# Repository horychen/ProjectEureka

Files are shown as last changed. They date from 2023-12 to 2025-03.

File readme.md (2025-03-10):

# ProjectEureka!--A Multi-phase Motor Drive Design for Robot or Maglev systems

ProjectEureka seeks to streamline the intricate design of robot systems, including communication, cable arrangements, and synchronization, by integrating several motor drivers (up to four) with a single microcontroller (DSP2837xD). This can also be utilized as a testing platform for bearingless motor or any other kind of AC motors. For access to example codes, please visit the following link: [here](https://github.com/horychen/ProjectPanGu-C) for cpu01 code, and [here](https://github.com/horychen/ProjectPanGuCpu2) for cpu02 code. Displayed below is an image representing the previous version.

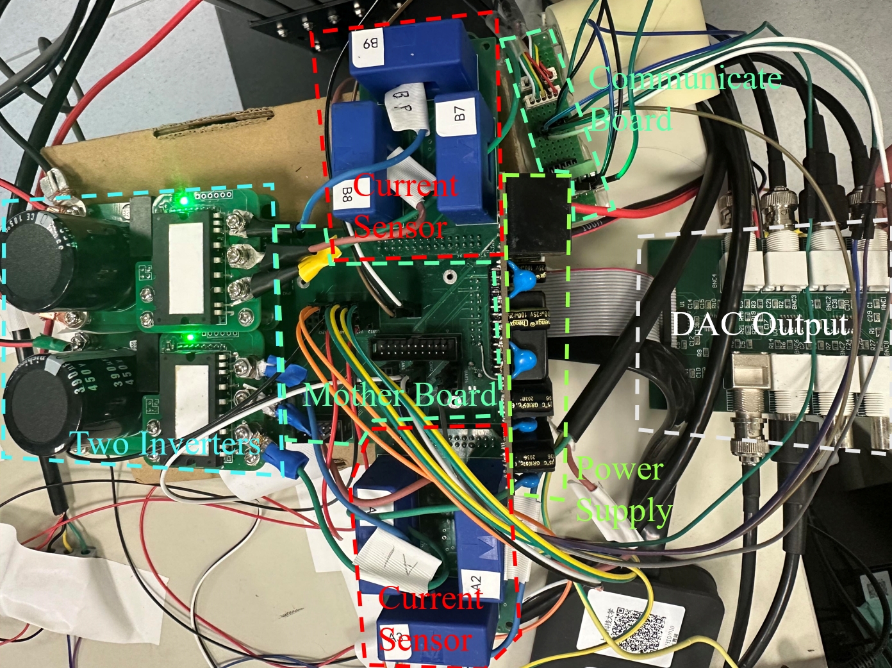
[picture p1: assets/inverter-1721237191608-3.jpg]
inverter-3d-view


## Software

We have been shifting from Altium Designer to KiCAD.

## Characteristics

**Multi-board modulized design is adopted in Project Eureka!.** Project Eureka! includes:

1. Current sensor(LA55-P) [📂 PCBProject_SensorLEM](PCBProject_SensorLEM)
2. DAC data collect board(MAX5725)[📂PCBProject_SPI_MAX5307_DAC](PCBProject_SPI_MAX5307_DAC)
3. RS422/RS423 communication board [📂PCBProject_Encoder](PCBProject_Encoder)
4. Inverters (FNC42060F) [📂PCBProject_InverterFNC42060F](PCBProject_InverterFNC42060F)
5. Auxiliary power supply [📂PCBProject_Power](PCBProject_Power)
6. Mother board that connected all the boards above [📂PCBProject_Extension28377dBGA](PCBProject_Extension28377dBGA)
7. CAN/SCI/USB communication board[📂PCBProject_Can_SCI_USB](PCBProject_Can_SCI_USB)
8. RS485 communication board [📂PCBProject_Happy485](PCBProject_Happy485)

This means:

1. Convenient alternative for replacing one's own projects or addressing shortages of components.
2. Utilize a single board design in their own design.
3. Quick update and easy for collaboration (KiCAD 8 supports git now).

**ProjectEureka can drive at most four AC motors.** Thanks to the TMS320F28377D from TI, ProjectEureka can drive at most four AC motors by adding necessary inverter blocks and corresponding current sensors, which means:

1. Facilitates communication and synchronization among motors.
2. Suitable for organizing cables in a user-friendly manner.

## Liscence
GPLv3

## Other Similar Projects

Odrive and VESC are two famous projects that support the control of a three-phase motor.
There are inverter designs that are compatible with them, see e.g., [Axiom](https://hackaday.io/project/164932-axiom-100kw-motor-controller). Other similar but less known hardwares can also be found, see e.g., [moteus-c1](https://jpieper.com/2024/04/30/moteus-c1/). Yet another project I recently found is [STMBL](https://github.com/rene-dev/stmbl?tab=readme-ov-file) for STM32 microprocessor.

ProjectEureka! is, however, focusing on the more advanced topic of a complicated system that requires extendable hardwares.
In this sense, there is indeed one similar purpose project that is based on Xilinx, i.e., [the AMDC platform from the group of Prof. Eric L. Severson](https://amdc.dev/). See also [its doc](https://docs.amdc.dev/getting-started/user-guide/host-interface/index.html) and [its blog post](https://severson.wempec.wisc.edu/2022/02/11/introducing-the-advanced-motor-drive-controller/).

As a comparison, ProjectEureka! currently only supports 28379D that has one CLB module of a very limited FPGA capability.

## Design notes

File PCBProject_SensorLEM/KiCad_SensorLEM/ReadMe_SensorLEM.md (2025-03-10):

# ReadMe_SensorLEM

下面这个是完整的驱动板，其中两条蓝色的器件是电流传感器，**<font color=red>左边</font>**的名称为对应到ProjectEureka\PCBProject_SensorLEM\KiCad_SensorLEM文件下的**<font color=red>SensorLEM1</font>**，然后**<font color=gree>右边</font>**的电流传感器对应到ProjectEureka\PCBProject_SensorLEM\KiCad_SensorLEM文件下的**<font color=gree>SensorLEM2</font>**。

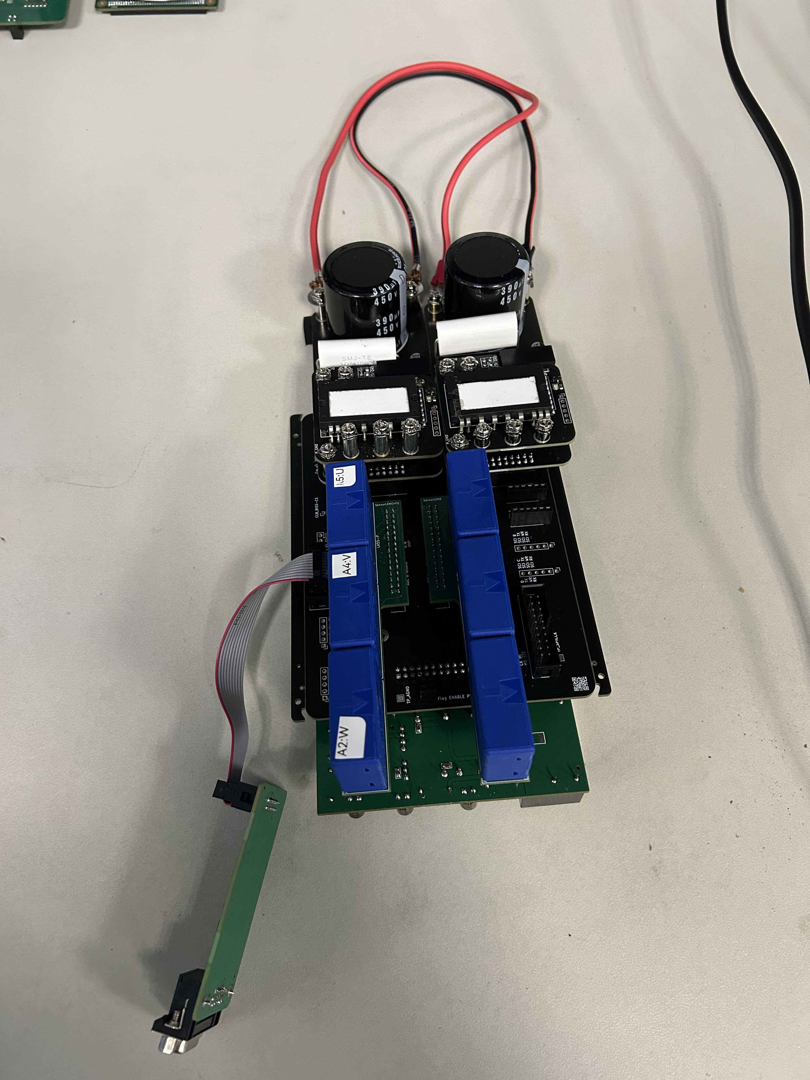
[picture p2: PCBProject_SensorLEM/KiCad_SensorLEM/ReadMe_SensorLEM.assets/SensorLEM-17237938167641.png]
SensorLEM


具体电路图就请看ProjectEureka\PCBProject_SensorLEM\KiCad_SensorLEM文件下的kicad文件。

****

<font color=red>我是红色</font>

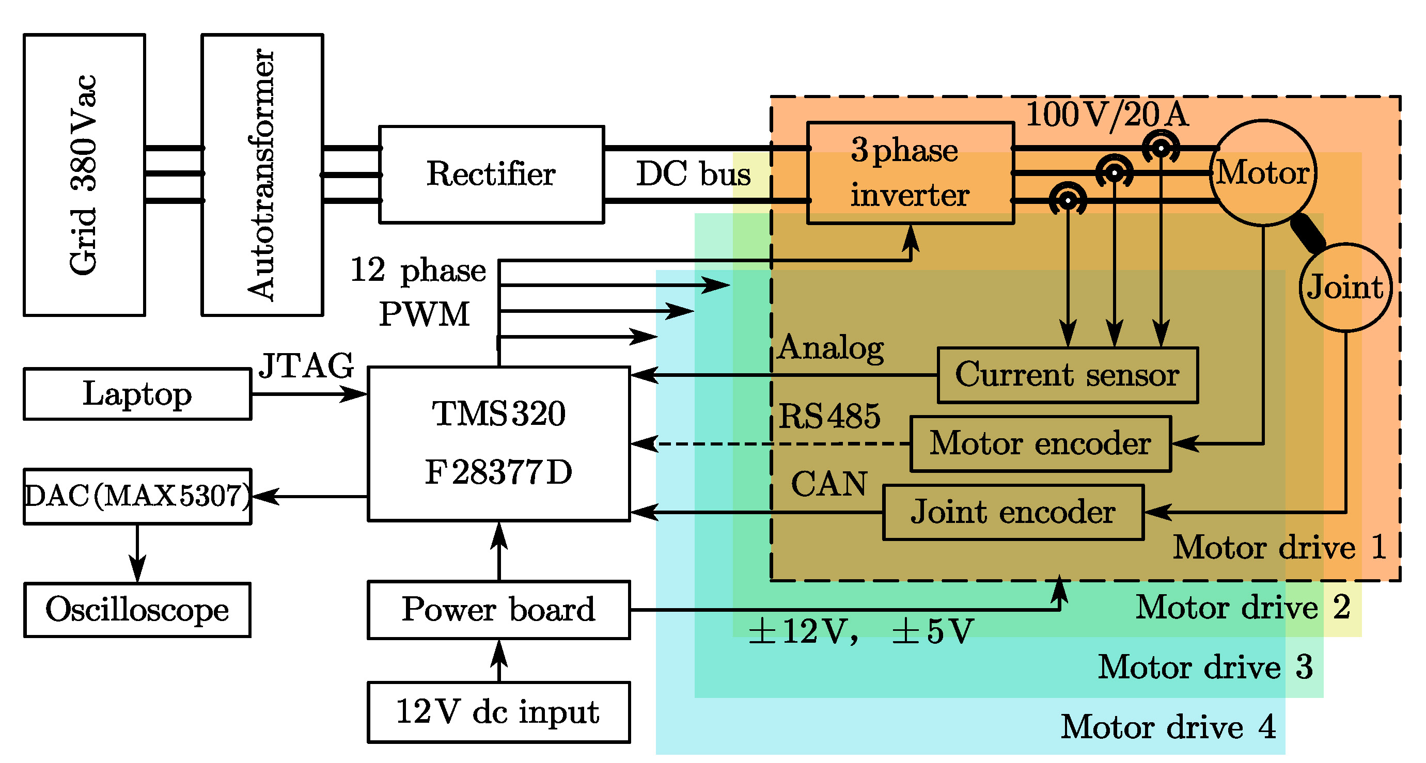
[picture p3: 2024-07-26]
assets/Block_Diagram.jpg

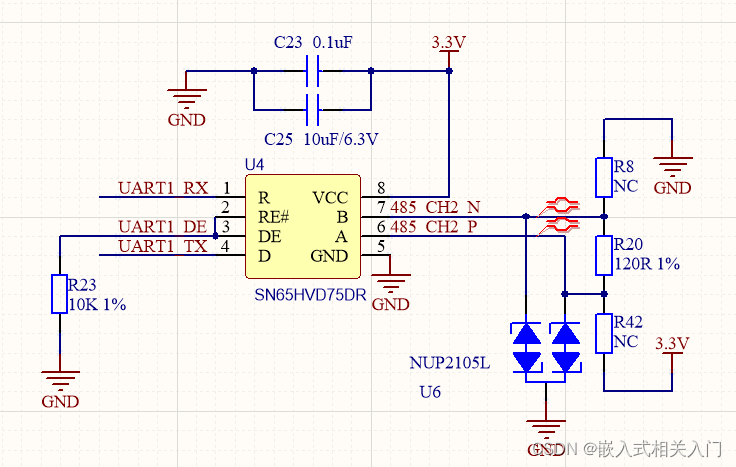
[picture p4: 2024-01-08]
PCBProject_Happy485/datasheet/野生原理图1.png

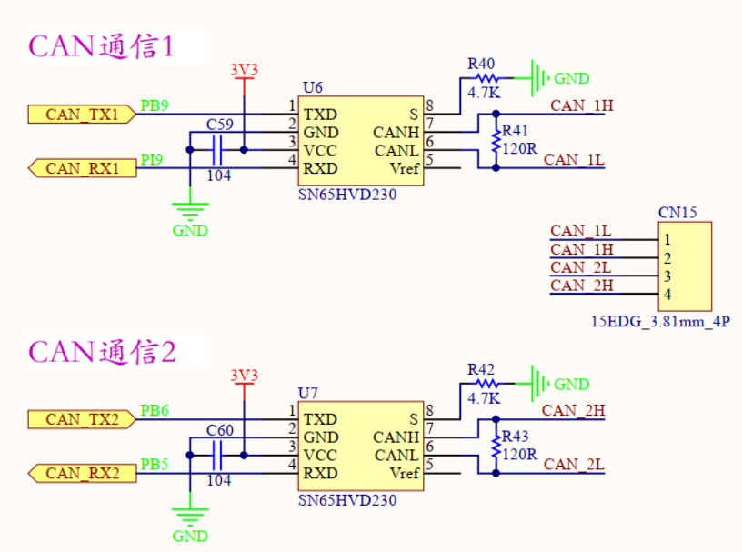
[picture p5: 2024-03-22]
PCBProject_Extension28377dBGA/ExtensionSimple2/Refs/CAN收发器SN65HVD230,实际应用案例分析.png

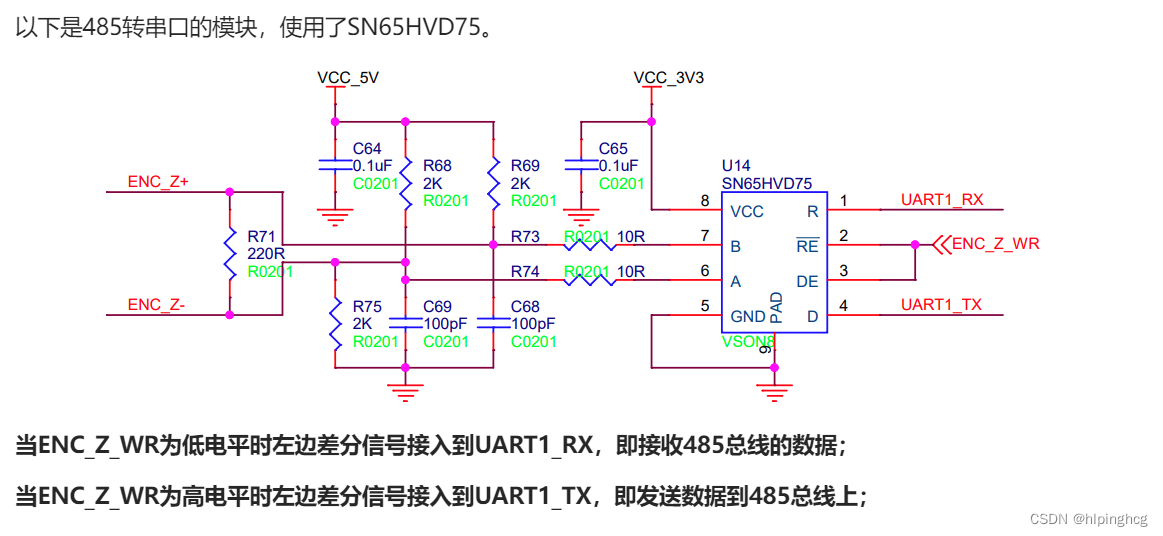
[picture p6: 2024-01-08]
PCBProject_Happy485/datasheet/野生原理图2.png

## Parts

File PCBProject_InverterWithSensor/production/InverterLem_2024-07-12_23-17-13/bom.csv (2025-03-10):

Designator | Footprint | Quantity | Value | LCSC Part #
+12 | TestPoint_Pad_D1.0mm | 1 | +12
+5v | TestPoint_Pad_D1.0mm | 1 | Test5V
-12 | TestPoint_Pad_D1.0mm | 1 | -12
15V | TestPoint_Pad_D1.0mm | 1 | Test15V
1A | TestPoint_Pad_D1.0mm | 1 | OPWM1A
1B | TestPoint_Pad_D1.0mm | 1 | OPWM1B
2A | TestPoint_Pad_D1.0mm | 1 | OPWM2A
2B | TestPoint_Pad_D1.0mm | 1 | OPWM2B
3A | TestPoint_Pad_D1.0mm | 1 | OPWM3A
3B | TestPoint_Pad_D1.0mm | 1 | OPWM3B
A1, A2, A3 | XDCR_LA55-P | 3 | LA55-P
A6 | VRB_S-6WR3 | 1 | VRB1215S-6WR3
AGND | TestPoint_Pad_D1.0mm | 1 | AGND
C1, C2, C3, C7, C8, C9 | 0603 | 6 | 47nf
C19, C59, C60, C61, C62 | CP_Radial_D16.0mm_P7.50mm | 5 | 47uF/450V
C20 | CP_EIA-3528-21_Kemet-B_Pad1.50x2.35mm_HandSolder | 1 | 15uF 50V Tantalum
C23 | 0603 | 1 | 10nF
C24 | 0603 | 1 | 1nf
C25 | CP_EIA-6032-28_Kemet-C_Pad2.25x2.35mm_HandSolder | 1 | 68uF 16V Tantalum
C27, C38, C39 | 0603 | 3 | 100nf
C4, C5, C6 | 0603 | 3 | 4.7uF
C40, C41, C42, C45, C46, C47 | 0603 | 6 | 2.2uf
C43, C44, C49, C54, C55, C57 | 0603 | 6 | 100pf
C48, C50, C51, C52, C56 | 0805 | 5 | 100nF
C53 | CP_Elec_6.3x7.7 | 1 | 100uf 50V
C58 | CP_Elec_5x5.4 | 1 | 22uf 25V
D1, D2 | D_SMA | 2 | 1N5819
D3 | 0805 | 1 | LEDRED
IC1, IC2, IC3 | SOIC-8_7.5x5.85mm_P1.27mm | 3 | TLP2270_D4-LF4,E
J1 | M3_smt | 1 | Phase 1
J2 | IDC-Header_2x10_P2.54mm_Vertical_SMD | 1 | DSP
J3 | M3_smt | 1 | Phase 2
J4 | M3_smt | 1 | Phase 3
J5 | PinSocket_1x02_P2.54mm_Vertical | 1 | Fan
J6 | M3_smt | 1 | DC_BUS
J7 | M3_smt | 1 | GND
J9 | PinSocket_1x02_P2.54mm_Vertical | 1 | Conn_01x02_Pin
L1 | L_6.3x6.3_H3 | 1 | 47uH
Q1 | FNC42060F | 1 | FNC42060F
Q2 | SOT-23-3 | 1 | FMMT618TA
R11, R12 | 0805 | 2 | 2M
R13, R14, R16, R21, R22, R23 | 0603 | 6 | 750R
R24, R25 | 2512 | 2 | 8mR
R26 | 1206 | 1 | 2k
R27, R28, R29, R30, R31, R32 | 0603 | 6 | 100R
R33, R34 | 0603 | 2 | 10K
R35 | 0603 | 1 | 2K
R36 | 0603 | 1 | 301R
RB1, RB2, RB3, RB4, RB5, RB6 | 0805 | 6 | 0R
U2 | SOIC-8_3.9x4.9mm_P1.27mm | 1 | LM2675M-5.0
Z1, Z2, Z3 | MELF_DO-213AB | 3 | ZM4746A-GS08

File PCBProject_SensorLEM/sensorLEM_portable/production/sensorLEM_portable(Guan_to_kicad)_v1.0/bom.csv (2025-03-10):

Designator | Footprint | Quantity | Value | LCSC Part #
A1, A4, A6 | SOT95P280X100-5N | 3 | LTC6240HV
A2, A3, A5 | XDCR_LA55-P | 3 | LA55-P
A7, A8 | VRB_S-6WR3 | 2 | VRB1215S-6WR3
BNC1, BNC2, BNC3 | BNC | 3 | BNC
C1, C15, C20, C3, C32, C34, C45 | 0805 | 7 | 105
C10, C12, C18, C24, C37, C38, C42, C48, C49, C54 | 0805 | 10 | 104
C11, C19, C23, C33, C41, C6 | 0805 | 6 | 47nf
C13, C14, C21, C26, C31, C39, C43, C44, C7 | 0805 | 9 | 103
C16, C2, C46, C5, C60 | CAP/6.4mm - | 5 | 100uf 25V 贴片铝电解
C17, C4, C47, C51, C8 | 1206 (钽电容) | 5 | 22uf 16V
C22, C40, C9 | 0805 | 3 | 101
C35, C36 | 1206 (钽电容) | 2 | 106 25V
C52, C55, C56 | 0805 | 3 | 102
D4 | l0805 | 1 | LED0
J1 | SHDR10W50P254_2X5_2020X850X920P | 1 | HIF3FC-10PA-2.54DSA_71_
J2, J3 | 接地柱M3 | 2 | Header 2
R1, R11, R13, R16, R6, R8 | 0805 | 6 | 20k
R10, R15, R4 | 0805 | 3 | 470R
R12, R14, R17, R3, R7, R9 | 0805 | 6 | 10k
R18 | 0805 | 1 | 1k
R19, R20, R21, RB1, RB2, RB3 | 0805 | 6 | 0R
RM1, RM2, RM3 | 2512 | 3 | 24R 1%精度
U1 | URB-YMD-15WR3 | 1 | URB2405YMD-15W
U2 | VRB_S-6WR3 | 1 | VRB1205S-6WR3
U4 | SOIC-8 | 1 | ADR423ARZ

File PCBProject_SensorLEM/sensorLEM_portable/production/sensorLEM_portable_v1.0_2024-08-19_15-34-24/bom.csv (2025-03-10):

Designator | Footprint | Quantity | Value | LCSC Part #
A1, A2, A3, A4, A5, A6 | LEM_LA 55-P | 6 | LA55-P
BNC1, BNC2, BNC3, BNC4, BNC5, BNC6 | CPBNCPC010 | 6 | BNC
C1, C15, C7, C8 | CAP-TH_L7.5-W4.5-P10.00-D0.6 | 4 | 1nF
C10, C14, C3, C5 | 0805 | 4 | 105
C11, C12, C16, C17, C18, C25, C26, C27, C31, C32, C33, C6 | 0805 | 12 | 47nf
C13, C2, C34, C4, C9 | CAP_6.4mm | 5 | 100uf 25V 贴片铝电解
C19, C20, C21, C22, C23, C24 | 0805 | 6 | 4.7uF
CN1 | CONN-TH_4P-P3.81_DB2EVC-3.81-4P | 1 | DB2EVC-3.81-4P-GN
D1 | LED0805 | 1 | LED0
R1, R19, R2, R20, R21, R3, RB1, RB10, RB11, RB12, RB2, RB3, RB4, RB5, RB6, RB7, RB8, RB9 | 0805 | 18 | 0R
R6 | 0805 | 1 | 4.7k
RM1, RM2, RM3, RM4, RM5, RM6 | 2512 | 6 | 24R 1%精度
U1, U2 | SIP,22x9.5mm | 2 | VRB1212S-6WR3
U3 | PWRM-TH_MORNSUN_FT-AX1D | 1 | FT-AX1D

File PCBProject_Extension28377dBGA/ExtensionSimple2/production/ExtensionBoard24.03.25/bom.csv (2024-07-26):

Designator | Footprint | Quantity | Value | LCSC Part #
C1, C15, C16, C2, C3, C4, C9 | 0805 | 7 | 104
C10, C11, C12 | 0805 | 3 | 103
C13, C14 | 0603 | 2 | 0.1uF
C5, C6, C7, C8 | 0805 | 4 | 102
CAN1, CAN2, SPI2, UART3, UART4 | PinSocket_2x04_P2.54mm_Vertical | 5 | Conn_02x04_Counter_Clockwise
D1, D2 | SOT-23 | 2 | BAR43S
D3 | 0805 | 1 | LEDRED
DI1 | PinSocket_2x02_P2.54mm_Vertical | 1 | Conn_02x02_Counter_Clockwise
DSP1 | DSP_240_SMD | 1 | ~
INC1, SPI1 | IDC-Header_2x10_P2.54mm_Vertical | 2 | HIF3FC-20PA-2.54DSA
IPM1, IPM2 | PinSocket_2x08_P2.54mm_Vertical | 2 | Conn_02x08_Top_Bottom
J1 | IDC-Header_2x05_P2.54mm_Vertical | 1 | Conn_02x05_Odd_Even
J2, J3 | PinSocket_2x02_P2.54mm_Vertical | 2 | Conn_01x02_Pin
J4 | PinSocket_1x05_P2.54mm_Vertical | 1 | CAN_1_CONNECT
J5 | PinSocket_1x04_P2.54mm_Vertical | 1 | RS485_1_CONNECT
J6 | PinSocket_1x05_P2.54mm_Vertical | 1 | CAN_2_CONNECT
J7 | PinSocket_1x04_P2.54mm_Vertical | 1 | RS485_2_CONNECT
LEM1, LEM2, POWER1 | PinSocket_2x15_P2.54mm_Vertical | 3 | HIF3FC-30PA-2.54DSA
N1 | SOIC14_M | 1 | MCP6024
Q1 | SOT-23 | 1 | FMMT618TA
R1, R10, R11, R12, R2, R3, R4, R48, R49, R5, R6, R7, R8, R9 | 0805 | 14 | 4.7k
R13, R14, R15, R16, RU3 | 0805 | 5 | 0R
R17, R18, R19, R20, R27, R28, R29, R32, R33 | 0805 | 9 | 10K
R21, R22, R24, R31 | 0805 | 4 | 1K
R23 | 0805 | 1 | 100R
R25 | 0805 | 1 | 1.69K/1%
R26 | 0805 | 1 | 3.3K/1%
R30 | 0805 | 1 | 2K
R34, R35, R39, R40, R41, R42, R46, R47 | 0603 | 8 | 10K
R36, R43 | 0603 | 2 | 120R
R37, R38, R44, R45 | 0402 | 4 | 10R
SCI_RS485_1, SCI_RS485_2 | SOIC127P600X175-8N | 2 | SN65HVD75D
TP1, TP10, TP11, TP12, TP2, TP3, TP4, TP5, TP6, TP7, TP8, TP9, VDC_BUS1, VDC_BUS2 | TestPoint_Pad_2.0x2.0mm | 14 | TP-黄色测试点
U1, U2 | TSSOP-20 | 2 | SN74ABT541
U4, U5 | SOIC-8_3.9x4.9mm_P1.27mm | 2 | SN65HVD230

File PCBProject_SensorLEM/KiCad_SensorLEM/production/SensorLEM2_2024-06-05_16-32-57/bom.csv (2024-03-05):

Designator | Footprint | Quantity | Value | LCSC Part #
A1, A3, A6 | SOT95P280X100-5N | 3 | LTC6240HV
A2, A4, A5 | XDCR_LA55-P | 3 | LA55-P
C1, C10, C18, C20, C27, C9 | 0805 | 6 | 105
C11, C13, C16, C2, C21, C25, C26, C4, C6 | 0805 | 9 | 103
C12, C23, C3 | 0805 | 3 | 101
C14, C15, C19, C22, C5, C7 | 0805 | 6 | 47nf
C17, C24, C8 | 0805 | 3 | 4.7uF
C28, C29 | 1206 (钽电容) | 2 | 106 25V
C30, C31 | 0805 | 2 | 104
J1 | SHDR30W50P254_2X15_4560X850X1200P | 1 | HIF3FC-30PA-2.54DSA
R10, R14, R18, R21, R3, R7 | 0805 | 6 | 10k
R11, R19, R4 | 0805 | 3 | 470R
R13, R17, R2, R20, R5, R9 | 0805 | 6 | 20k
RB1, RB2, RB3, RB4, RB5, RB6, RB7, RB8, RB9 | 0805 | 9 | 0R
RM1, RM2, RM3 | 2512 | 3 | 24R 1%精度
TP10, TP11, TP2, TP3, TP5, TP6, TP7, TP8, TP9 | TestPoint_THTPad_D2.0mm_Drill1.0mm | 9 | TP-黄色测试点
U1 | SOIC-8 | 1 | ADR423ARZ

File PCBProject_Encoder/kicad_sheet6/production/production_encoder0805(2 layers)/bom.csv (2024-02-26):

Designator | Footprint | Quantity | Value | LCSC Part #
AGND1, PEGND1, TP1, TP2, TP3, TP4, TP5, TP6 | TestPoint_Pad_2.5x2.5mm | 8 | IV黄色测试点
C1, C2, C3, C4, C5, C6 | 0805 | 6 | 103
C10, C11, C12, C13, C14, C15, C16, C17, C18, C28, C29, C30, C31, C32, C33, C7, C8, C9 | 0805 | 18 | 102
C19, C20, C26 | 0805 | 3 | 104
C21, C22, C23, C24, C25, C27 | 0805 | 6 | 101
J1 | DSUB-15-HD_Female_Horizontal_P2.29x1.98mm_EdgePinOffset3.03mm_Housed_MountingHolesOffset4.94mm | 1 | L77HDE15SD1CH4RHNVGA
J2 | IDC-Header_2x05_P2.54mm_Vertical | 1 | HIF3FC-10PA-2.54DSA
R1, R2, R3, R4, R5, R6 | 0805 | 6 | 241
R10, R11, R12, R13, R14, R15, R16, R17, R18, R7, R8, R9 | 0805 | 12 | 1001R
R19, R20, R21, R22, R23, R24 | 0805 | 6 | 1K
RK1, RK2, RK3 | 0805 | 3 | 0R
U1, U2 | SOIC127P600X175-16N | 2 | DS3486M
U3 | SOIC127P600X175-16N | 1 | SN74HC365D

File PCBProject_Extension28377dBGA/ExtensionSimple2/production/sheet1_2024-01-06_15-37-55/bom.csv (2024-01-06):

Designator | Footprint | Quantity | Value | LCSC Part #
C1, C2, C3, C4, C9 | 0805 | 5 | 104
C10, C11, C12 | 0805 | 3 | 103
C5, C6, C7, C8 | 0805 | 4 | 102
CAN1, CAN2, SPI2, UART1, UART2, UART3, UART4 | PinSocket_2x04_P2.54mm_Vertical | 7 | Conn_02x04_Counter_Clockwise
D1, D2 | SOT-23 | 2 | BAR43S
D3 | 0805 | 1 | LEDRED
DI1 | PinSocket_2x02_P2.54mm_Vertical | 1 | Conn_02x02_Counter_Clockwise
DSP1 | DSP_240_SMD | 1 | ~
INC1, SPI1 | IDC-Header_2x10_P2.54mm_Vertical | 2 | HIF3FC-20PA-2.54DSA
IPM1, IPM2 | PinSocket_2x08_P2.54mm_Vertical | 2 | Conn_02x08_Top_Bottom
J1 | IDC-Header_2x05_P2.54mm_Vertical | 1 | Conn_02x05_Odd_Even
J2, J3 | PinSocket_2x02_P2.54mm_Vertical | 2 | Conn_01x02_Pin
LEM1, LEM2, POWER1 | PinSocket_2x15_P2.54mm_Vertical | 3 | HIF3FC-30PA-2.54DSA
N1 | SOIC14_M | 1 | MCP6024
Q1 | SOT-23 | 1 | FMMT618TA
R1, R10, R11, R12, R2, R3, R4, R5, R6, R7, R8, R9 | 0805 | 12 | 4.7k
R13, R14, R15, R16, RU3 | 0805 | 5 | 0R
R17, R18, R19, R20, R27, R28, R29, R32, R33 | 0805 | 9 | 10K
R21, R22, R24 | 0805 | 3 | 1k
R23 | 0805 | 1 | 100R
R25 | 0805 | 1 | 1.69K/1%
R26 | 0805 | 1 | 3.3K/1%
R30 | 0805 | 1 | 2K
R31 | 0805 | 1 | 301R
TP1, TP10, TP11, TP12, TP2, TP3, TP4, TP5, TP6, TP7, TP8, TP9, VDC_BUS1, VDC_BUS2 | TestPoint_Pad_2.0x2.0mm | 14 | TP-黄色测试点
U1, U2 | TSSOP-20 | 2 | SN74ABT541

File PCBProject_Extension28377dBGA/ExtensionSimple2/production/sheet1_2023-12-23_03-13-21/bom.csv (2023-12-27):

Designator | Footprint | Quantity | Value | LCSC Part #
AGND1, TP11, TP12, TP15, TP16, TP19, TP20, TP23, TP24, TP27, TP28, TP5, TP6, VDC_BUS1, VDC_BUS2 | TestPoint_Pad_2.0x2.0mm | 15 | TP-黄色测试点
C2, C39, C4, C40 | 0402 | 4 | 103
C25, C26, C37, C7, C8, C9 | 0402 | 6 | 104
C30, C31, C34, C35 | 0402 | 4 | 102
CAN1, CAN2, SPI2, UART1, UART2, UART3, UART4 | PinSocket_2x04_P2.54mm_Vertical | 7 | Conn_02x04_Counter_Clockwise
D1 | 0805 | 1 | LEDRED
D10, D12, D13, D14, D24, D25, D8, D9 | SOT-23 | 8 | BAR43S
DI1 | PinSocket_2x02_P2.54mm_Vertical | 1 | Conn_02x02_Counter_Clockwise
INC1, INC2, SPI1 | IDC-Header_2x10_P2.54mm_Vertical | 3 | HIF3FC-20PA-2.54DSA
LEM1, LEM4 | IDC-Header_2x15_P2.54mm_Vertical | 2 | HIF3FC-30PA-2.54DSA
N2 | SOIC14_M | 1 | MCP6024
P1 | DSP_240 | 1 | TMS320F28377D-BGA-Core
P10, P11, P12, P19, P20, P21, P22, P9 | PinSocket_2x02_P2.54mm_Vertical | 8 | Header 2X2
P13, P14 | PinSocket_2x06_P2.54mm_Vertical | 2 | Header 6X2
POWER1 | PinSocket_2x15_P2.54mm_Vertical | 1 | HIF3FC-30PA-2.54DSA
Q2 | SOT-23 | 1 | FMMT618TA
R1, R2 | 0402 | 2 | 100R
R13 | 0402 | 1 | 3,.3K
R15, R16, R19, R20, R23, R24, R27, R28, R41, R42, R47, R48 | 0402 | 12 | 4.7k
R30 | 0402 | 1 | 301R
R32, R80, R81, R84, R85, R91, R92, R93, R94 | 0402 | 9 | 10K
R34 | 0402 | 1 | 2K
R6 | 0402 | 1 | 1.69K
R73, R74, R75, R76 | 0805 | 4 | 0R
R8, R88, R89, R9 | 0402 | 4 | 1K
U2, U3 | TSSOP-20 | 2 | SN74ABT541
U4 | SOIC127P600X175-16N | 1 | SN74HC365D
USB1 | PinSocket_2x10_P1.27mm_Vertical | 1 | HIF3FC-20PA-2.54DSA

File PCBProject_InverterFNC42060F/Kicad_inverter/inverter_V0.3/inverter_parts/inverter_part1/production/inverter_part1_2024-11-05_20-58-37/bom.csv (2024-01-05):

Designator | Footprint | Quantity | Value | LCSC Part #
A1 | VRB_S-6WR3 | 1 | VRB1215S-6WR3
C1, C2, C3 | 0603 | 3 | 100nf
C22, C24 | 0805 | 2 | 100nF
C23 | CP_Elec_6.3x7.7 | 1 | 100uf 50V
C25 | CP_Elec_5x5.4 | 1 | 22uf 25V
C34 | 0603 | 1 | 10nF
C35 | CP_EIA-3528-21_Kemet-B_Pad1.50x2.35mm_HandSolder | 1 | 15uF 50V Tantalum
C36 | CP_EIA-6032-28_Kemet-C_Pad2.25x2.35mm_HandSolder | 1 | 68uF 16V Tantalum
C4 | CP_Radial_D35.0mm_P10.00mm_SnapIn | 1 | 390uF/450V
D2, D4 | D_SMA | 2 | 1N5819
IC1, IC2, IC3 | SOIC-8_7.5x5.85mm_P1.27mm | 3 | TLP2270_D4-LF4,E
J1 | PinSocket_2x08_P2.54mm_Vertical | 1 | Conn_02x06_Top_Bottom
J14, J15, J17, J6, J7 | M3_smt | 5 | Header 2
J3 | PinSocket_1x08_P2.54mm_Vertical | 1 | Conn_01x08_Pin
J4, J5 | PinSocket_2x02_P2.54mm_Vertical | 2 | Conn_01x02_Pin
L2 | L_6.3x6.3_H3 | 1 | 47uH
R1, R2, R4, R5, R8, R9 | 0603 | 6 | 750R
R10, R11 | 0805 | 2 | 2M
TP7 | TestPoint_Pad_D1.0mm | 1 | Test15V
TP8 | TestPoint_Pad_D1.0mm | 1 | Test5V
U2 | SOIC-8_3.9x4.9mm_P1.27mm | 1 | LM2675M-5.0

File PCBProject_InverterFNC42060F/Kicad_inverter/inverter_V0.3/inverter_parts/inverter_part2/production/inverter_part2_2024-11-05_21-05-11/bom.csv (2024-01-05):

Designator | Footprint | Quantity | Value | LCSC Part #
C10, C12, C13, C5, C6, C9 | 0805 | 6 | 2.2uf
C11, C14, C7 | 0805 | 3 | 100nf
C15, C16, C17, C18, C19, C20 | 0603 | 6 | 100pf
C21 | 0603 | 1 | 1nf
D1 | 0805 | 1 | LEDRED
H1, H2, H3 | MountingHole_3.2mm_M3_Pad_Via | 3 | MountingHole_Pad
J10 | PinSocket_1x06_P2.54mm_Vertical | 1 | Conn_01x06_Pin
J11, J8, J9 | M3_smt | 3 | Header 2
J12 | PinSocket_2x02_P2.54mm_Vertical | 1 | Conn_01x02_Pin
J13 | PinSocket_1x02_P2.54mm_Vertical | 1 | Conn_01x02_Pin
J2 | PinSocket_1x08_P2.54mm_Vertical | 1 | Conn_01x08_Pin
Q1 | SOT-23-3 | 1 | FMMT618TA
Q2 | FNC42060F | 1 | FNC42060F
R13, R14, R15, R16, R17, R18 | 0603 | 6 | 100R
R19, R20 | 2512 | 2 | 8mR
R21 | 1206 | 1 | 2k
R22 | 0603 | 1 | 1K
R3 | 0805 | 1 | 301R
R6 | 0603 | 1 | 10K
R7 | 0603 | 1 | 2K
Z1, Z2, Z3 | MELF_DO-213AB | 3 | ZM4746A-GS08

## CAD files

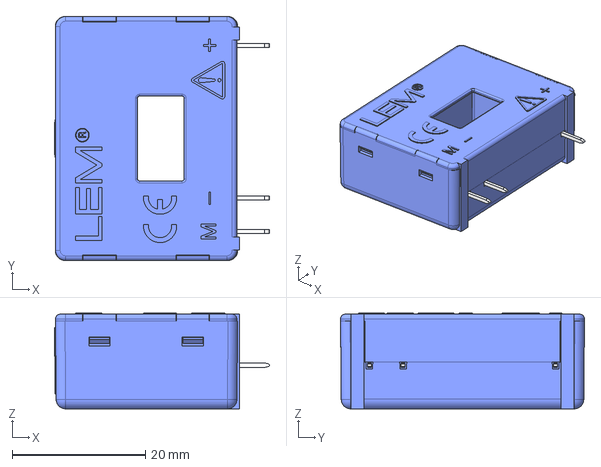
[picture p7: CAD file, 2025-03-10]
PCBProject_InverterWithSensor/LA55P.stp
32.3 x 36.6 x 14.4 mm

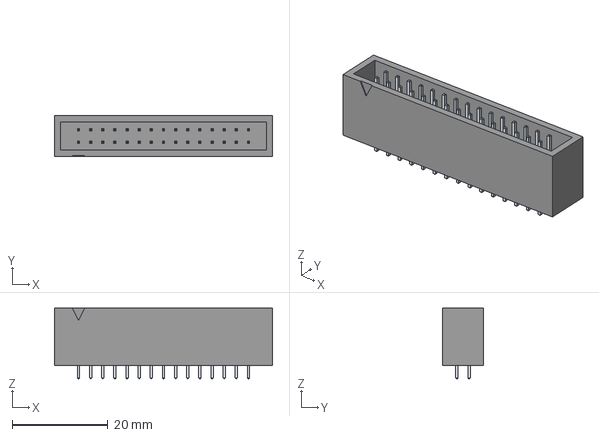
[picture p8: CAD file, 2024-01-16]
PCBProject_SensorLEM/ALTIUM_EMBEDDED_MODELS/HIF3FC-30PA-2.54DSA_71_.stp
45.6 x 8.50 x 14.8 mm
LeadsArray

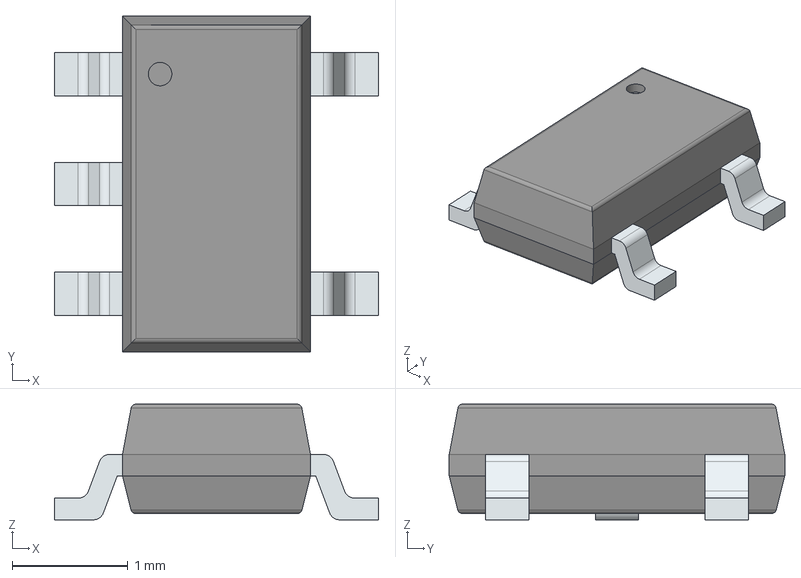
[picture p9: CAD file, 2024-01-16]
PCBProject_SensorLEM/SensorLEM_Guan/ALTIUM_EMBEDDED_MODELS/LTC6240HVCS5#TRMPBF.stp
2.80 x 2.90 x 1.00 mm
PinsArrayL
PinsArrayR

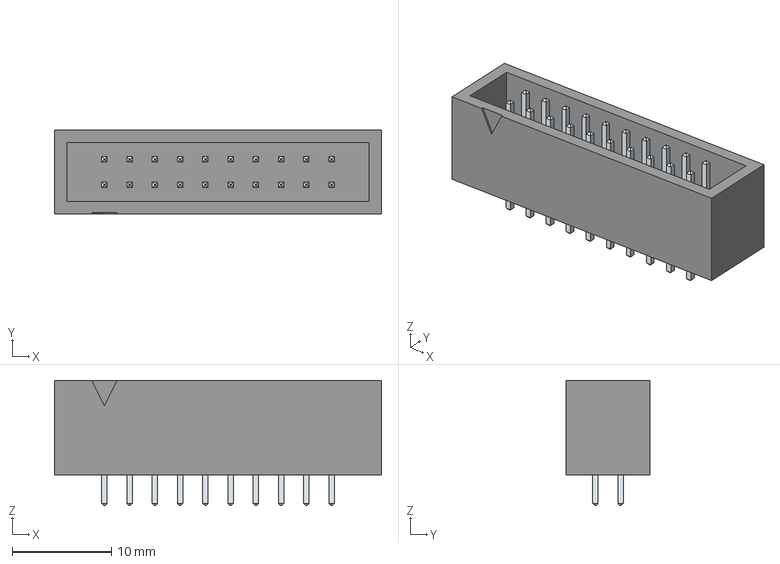
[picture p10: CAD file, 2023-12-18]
PCBProject_SPI_MAX5307_DAC/ALTIUM_EMBEDDED_MODELS/HIF3FC-20PA-2.54DSA_71_.stp
32.9 x 8.50 x 12.6 mm
LeadsArray

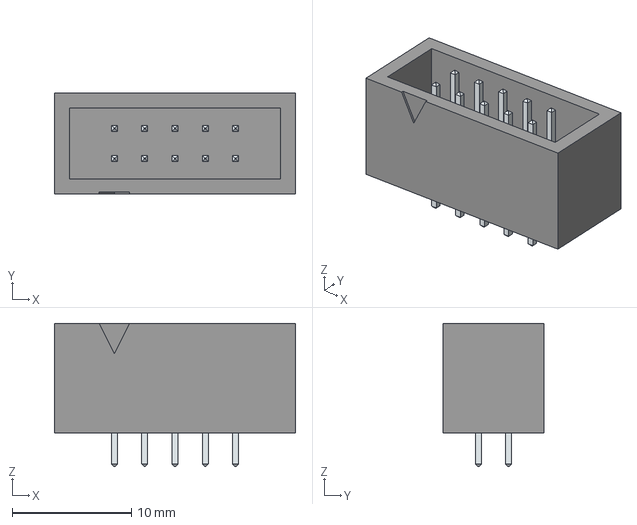
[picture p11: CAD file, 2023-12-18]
PCBProject_SensorLEM/SensorLEM_Guan/ALTIUM_EMBEDDED_MODELS/HIF3FC-10PA-2.54DSA_71_.stp
20.2 x 8.50 x 12.0 mm
LeadsArray

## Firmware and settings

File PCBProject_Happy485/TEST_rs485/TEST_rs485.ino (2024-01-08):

#include <Arduino.h>
bool receive_TAG = 0;
bool request_TAG = 0;
char data_receive[10] ;
int Index = 0;
void setup() {
  // put your setup code here, to run once:
  Serial1.setTX(16);
  Serial1.setRX(17);
  Serial1.begin(2500000);
  pinMode(5, OUTPUT); 
  digitalWrite(5, LOW);
  Serial.begin(9600);
  Serial.println("HELLO");
}


void loop() {
  if(Serial.available()){
    request_TAG = 1;
    Serial.read();
  }
  if(request_TAG){
    digitalWrite(5, HIGH);
    Serial.println("request once");
    delayMicroseconds(2);
    Serial1.write(0x02);
    Serial1.flush();
    digitalWrite(5, LOW);
    request_TAG = 0;
  }
  while(Serial1.available()){
    data_receive[Index] = Serial1.read();
    Index++;
    receive_TAG = 1;
  }
  Index = 0;
  if(receive_TAG){
    receive_TAG = 0;
    long pos = long(data_receive[4] << 12) + long(data_receive[3] << 4) + long(data_receive[2] >> 4 );
    double angle = pos * 360 / 524288.0;
    Serial.println("get angle:");
    Serial.println(pos);
    Serial.println(angle, 6);
  }
  
  // put your main code here, to run repeatedly:
  
}

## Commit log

2023-12-11 add spi-can and encoder boards
    [Project4_Encoder.PrjPcb, Project5_SPI_MAX5307_DAC.PrjPcb, Project6_VoltageSensorCard.PrjPcb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]
2023-12-12 change power supp;y to 12 and maintain 15 pulgin
    [sheet3.SchDoc]
2023-12-12 power schematic finished
    [1_P1.schdoc.SCHLIB, project0_Power.PrjPcb, sheet0.SchDoc]
2023-12-13 finish inverter PCB in kicad
    [600V_20A_MotorController_V2.0.PcbDoc, 600V_20A_MotorController_V2.0.SchDoc, inverter.kicad_pcb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]
2023-12-13 update sheet1
    [sheet1.SchDoc]
2023-12-13 add REF_3V
    [PCB3.PcbDoc, sheet3.SchDoc]
2023-12-13 position changes
    [PCB3.PcbDoc]
2023-12-14 Power PCB finished
    [1_P1.schdoc.SCHLIB, PCB0.PcbDoc, PCBProject_AdapterBoard_NTUInv.PrjPcb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]
2023-12-14 sheet1 add PWM.
    [sheet1.SchDoc]
2023-12-14 Update sheet3 12VGND.
    [project0_Power.PrjPcb, sheet1.SchDoc, sheet3.SchDoc]
2023-12-14 YZZ: update the power names.
    [sheet0.SchDoc, sheet1.SchDoc]
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2023-12-14 remove +-15V add 12VGND
    [PCB3.PcbDoc, sheet3.SchDoc]
2023-12-15 sheet1 add power
    [sheet1.SchDoc]
2023-12-15 Update Power PCB, this is final version
    [PCB0.PcbDoc, sheet0.SchDoc]
2023-12-15 Update extension
    [sheet1.SchDoc]
2023-12-16 extensionBoard again
    [sheet1.SchDoc]
2023-12-16 update inverter board
    [inverter.kicad_pcb, inverter.kicad_sch, inverter_2in1.kicad_pcb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]
2023-12-17 update Extension sch, kicad version
    [Extension.kicad_pcb, Extension.kicad_sch, sheet1.kicad_sch]
2023-12-17 Update Power board, PDN is failed
    [OdbCache.cfg, PCB0.PcbDoc, project0_Power.PrjPcb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]
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2023-12-18 update sheet1 (kicad)
    [sheet1.kicad_sch]
2023-12-18 add footprint again(
    [HIF3FC-10PA-2.54DSA_71_.stp, HIF3FC-20PA-2.54DSA_71_.stp]
2023-12-20 Add sheet pcb.
    [Extension.kicad_pcb, Extension.kicad_sch, sheet1.kicad_pcb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]
2023-12-20 Place the components.
    [sheet1.kicad_pcb]
2023-12-20 Add ExtensionSimple board for fast prototyping.
    [sheet1.kicad_pcb, sheet1.kicad_sch]
2023-12-23 New kicad library and send sheet1 for production.
    [bom.csv, designators.csv, positions.csv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]
2023-12-27 fix bugs in power and LEM boards
    12VGND should be negative input to amp on LEM. May be also need single connected?
    [PCB0.PcbDoc, bom.csv, designators.csv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]
2024-01-03 Add ExtensionSimple2
    [bom.csv, designators.csv, positions.csv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]
2024-01-04 comnponents kayout in the pcb
    [sheet1.kicad_pcb]
2024-01-04 Components layout
    [sheet1.kicad_pcb]
2024-01-05 block routing done.
    [sheet1.kicad_pcb, sheet1.kicad_sch]
2024-01-05 update inverter board version 0.2
    [inverter_conn.kicad_sch, inverter_power.kicad_pcb, inverter_power.kicad_sch]
2024-01-05 cross check of invterter
    [inverter_power.kicad_pcb, inverter_power.kicad_sch]
2024-01-05 add inverter board production files
    [bom.csv, designators.csv, inverter_board1.kicad_pcb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]
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2024-01-05 extension board layout
    [sheet1.kicad_pcb, sheet1.kicad_sch]
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2024-01-05 HY加油
    [sheet1.kicad_pcb, sheet1.kicad_sch]
2024-01-05 Revert "HY加油"
    This reverts commit aaa1912d429fb000e99d7c8797d7335188b5b639.
    rollback
    [sheet1.kicad_pcb, sheet1.kicad_sch]
2024-01-05 Power layout
    [sheet1.kicad_pcb]
2024-01-05 HY finished layout GND铺铜
    [sheet1.kicad_pcb]
2024-01-06 extension Update
    need double check
    [sheet1 - Copy.kicad_sch, sheet1.kicad_pcb]
2024-01-06 submit extension board
    [bom.csv, designators.csv, positions.csv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]
2024-01-06 add sheet6 encoder kicad files.
    [PA_Encoder.SchDoc, bom.csv, designators.csv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]
2024-01-08 add RS485 board to project
    [rs485_SN65HVD75_TestBoard.kicad_pcb, rs485_SN65HVD75_TestBoard.kicad_sch]
2024-01-15 add sheet6 encoder board provided by wang, qian
    [bom.csv, designators.csv, kicad_sheet6.kicad_pcb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]
2024-01-16 alter encoder, making it better.
    [HIF3FC-20PA-2.54DSA_71_.stp, HIF3FC-30PA-2.54DSA_71_.stp, LTC6240HVCS5#TRMPBF.stp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]
2024-01-19 改善编码器
    [kicad_sheet6.kicad_sch]
2024-01-29 重新布线+原图备份x1
    [kicad_sheet6.kicad_pcb, kicad_sheet6.kicad_sch]
2024-01-29 01.29pcb更改
    [kicad_sheet6.kicad_pcb]
2024-02-21 corrret Extension size
    [sheet1.kicad_pcb, sheet1.kicad_sch]
2024-02-22 correct Extension-IPM1 size
    [sheet1.kicad_pcb]
2024-02-25 renew Encoder--kicad_sheet6
    [kicad_encoder.kicad_pcb, kicad_sheet6.kicad_pcb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]
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2024-03-12 add some text items
    [sheet1.kicad_pcb, sheet1.kicad_sch]
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2024-03-25 Update ExtensionSimple3 schematic and pcb
    [sheet1.kicad_pcb, sheet1.kicad_sch]
2024-03-30 finish DACBoard and redefine the pins of DACBoard
    [pcb5.kicad_pcb, pcb5.kicad_sch, sheet1.kicad_sch]
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2024-04-01 Fix Teardrop
    [sheet1.kicad_pcb]
2024-04-03 @Eorl 1. 需要第二套高速SPI，把 SPI-A 引出来用于DSP之间50MHz通讯。 2. 给I2C找到合适的GPIO引脚，更新原理图 3. 随便找一排GPIO引脚拉到2.54mm的排针上，为INPUT-XBAR预留 4. CAN的12V电源应该是数字电源，现在是用电流传感器的12V，not good 5. CAN排针之间太近，485排针之间太近 6. QEP不需要那个2*10的简牛，删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
    [sheet0.SchDoc, sheet1.kicad_pcb, sheet1.kicad_sch]
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2024-04-14 fix some extension bugs
    [sheet1.kicad_pcb]
2024-04-19 let VDD to 485
    [sheet1.kicad_pcb, sheet1.kicad_sch]
2024-04-25 fix VDD and ref_3V, DC_bus location
    [pcb5.kicad_sch, sheet1.kicad_pcb, sheet1.kicad_sch]
2024-06-05 update sensorlem2(right) to adapt to extensionborad3
    [SensorLEM(Yan).kicad_pcb, SensorLEM(left_Copied).kicad_pcb, SensorLEM(right).kicad_pcb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]
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2024-07-26 pull the remote library to the local location
    [InverterLem.kicad_pcb, InverterLem.kicad_sch, LA55P.stp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]
2024-08-17 SensorLEM: Add sensorLEM_portable file(From Altium Designer file 'SensorLEM_Guan' to Kicad).
    [HIF3FC-10PA-2.54DSA_71_.stp, LTC6240HVCS5#TRMPBF.stp, PCB3.PcbLib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]
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2024-11-06 Inverter：Generating .zip of Inverter for LichuangEDA.
    [bom.csv, designators.csv, positions.csv]
